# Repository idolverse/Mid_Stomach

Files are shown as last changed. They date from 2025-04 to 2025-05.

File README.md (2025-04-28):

<h1>中腹部：</h1>

本教程是关于中腹部部分的组装。

**注意** ，一旦腿做好了，这些部件肯定会被淘汰，而且是临时的。我还是把它们贴出来了，因为很多建造者都要求。这个教程里缺少图片，我把它们和硬盘一起弄丢了……

在打印所有部件之前，您应该打印一份校准器 (CALIBRATOR)，以检查部件是否能够拼合。如果您在拼合这些部件时遇到困难，可以调整切片软件的水平扩展设置来解决这个问题。此设置可能因切片机和打印机而异，但用户报告称，将其设置为 -0.15 是一个不错的起点。

填充率为 30%，壁厚为 2.5 毫米，最好无筏，无支撑（除非另有说明），大部件使用边缘以避免翘曲。

您需要打印以下所有部分：

1x BotBackLeft

1x BotBackRigt

1x BotCapLeft

1x BotCapRight

1x BotFrontLeft

1x BotFrontRigt

1x HipCoverFront

1x HipCoverLeft

1x HipCoverRight

1x MidPotHolder

2x MidWormRight

你需要两个 HS-805bb 舵机，需要进行破解。两个舵机只使用一块舵机板和一个电位器，这样两个电机就能同步旋转。教程中会详细解释这一点。

你需要65到70个滚珠轴承。你可以使用钢珠或BB枪珠。它们的直径应为6毫米。

我尝试使用Vigor VSD-11AYMB舵机，并制作了一些适合它的文件。可惜的是，这些舵机性能不佳，有时会抖动。另一个恼人的问题是，它们无法通过软件正确“分离”。

视频：https://youtu.be/9G8FDBgAxu0?t=3

<h2>步骤1：</h2>

DSC06884-600x450

检查StomGearV2.stl是否正确适合上腹部部件。



还要确保StoGearAttachV1.stl牢固地固定在 Top Stomach 部件的底面上。更多信息请查看TopStomach 教程。

<h2>步骤2：</h2>



将BotBackLeftV1.stl、BotBackRigtV1.stl、BotFrontLeftV1.stl、BotFrontRigtV1.stl组装在一起。

DSC06826-600x450

最好将它们粘在一起放在平坦的表面上。

DSC06830-600x450

对于有此需要的用户，还可以选择安装螺栓。

DSC06827-600x450

确保平面尽可能平坦。

DSC06836-600x450

如果表面太不平整，请将一张带有双面胶带的砂纸粘在平板上，然后打磨组件，直到满意为止。

DSC06886-600x450

将安装滚珠轴承的表面打磨光滑。我个人使用了丙酮，因为我的零件是用ABS打印的。



切断HipCoverFrontV1.stl上的预支撑。



用3毫米螺丝将HipCoverFrontV1.stl安装到你的组件上。我使用遮蔽胶带给黑色部分喷涂了汽车哑光喷漆。

DSC06887-600x450

用螺丝将两个MidWormRightV1.stl文件安装  到舵机摇臂上。用木螺钉将舵机安装到组件上。舵机的连接线将在后面的步骤 3中详细说明。

在此阶段，最好确保 StomGear 能够很好地与您的组件匹配。

DSC06888-600x450

在蜗轮上和 StomGear 的通孔中涂上适量的油脂。

DSC06890-600x450

检查 StomGear 上的电位器孔并将其放置在如图所示的位置。

DSC06891-600x450

适合 StomGear。

DSC06892-600x450

让它在整个组装过程中顺利进行。

<h2>步骤3：</h2>

破解伺服系统

您需要按照本教程中的说明从舵机上移除电位器。请记住，Vigor VSD-11AYMB 舵机与 Hitec805BB 舵机略有不同。以下教程针对 Hitec805BB 舵机进行说明。

需要对两个伺服器进行破解才能使其连续旋转。

两个伺服器中的一个将由另一个控制，因此您必须移除该伺服器的电路板和电位器（请妥善保管以备备用，以防有一天您烧毁了 805B 伺服器控制板）。



拆除三处焊接，拆下伺服控制板和方形电位器



将两根电线直接焊接在电机上，红点代表正极（我猜）。



并像往常一样切割阻碍伺服电机完全旋转的小块。

DSC07259-600x450

将蓝色电缆设置在电机正极侧（红点）

DSC07258-600x450

在另一个电机上，将棕色电缆设置在电机的正极侧。（红点）

DSC07257-600x450

确保已将彩色电缆与电机极性反转。这样，一个电机会朝一个方向旋转，另一个电机也会朝另一个方向旋转。

<h2>步骤4：</h2>

缺失图片：将BotCapLeftV1.stl和BotCapRightV1.stl在平面上组装在一起。如果打印 ABS，请使用丙酮；如果打印 PLA，请使用环氧树脂。

DSC06889-600x450

将电位器安装在MidPotHolderV1.stl上，并注意与小型金属定位器的位置。将MidPotHolderV1.stl粘贴到 BotCap 上。

DSC06893-600x450

将 BotCap 组件设置在主组件上。

 DSC06894-600x450

使用 4 毫米螺丝将 BotCap 固定到主组件上。

DSC06897-600x450

将TStoLowLeftV1.stl和TStoLowRightV1.stl  安装到主组件。



使用夹具压配合将使工作变得轻松。



安装 4 毫米螺钉，确保螺钉头完全嵌入部件。否则会限制上腹部和中腹部之间的旋转。

DSC06902-600x450

在侧面也添加螺丝。

<h2>步骤5：</h2>

DSC06906-600x450

在装配平板上添加适量油脂。



添加一些 6 毫米滚珠轴承，我使用了 BB 枪球，到目前为止效果很好。

DSC06909-600x450

在 TopStomach 的平板上也涂抹油脂。



安装 StomGear 以将 TopStomach 和 MidStomach 组装在一起。

DSC06912-600x450

使用 4 颗 4mm 螺丝将 StomGearV2.stl固定到StoGearAttachV1.stl ，如Top Stomach 教程中所示

DSC06913-600x450

调整螺栓，确保上腹部和中腹部紧固。但不要拧得太紧，因为我们希望这些部件能够有一定的旋转自由度。

现在是时候运行一些脚本测试来查看是否一切设置好了。

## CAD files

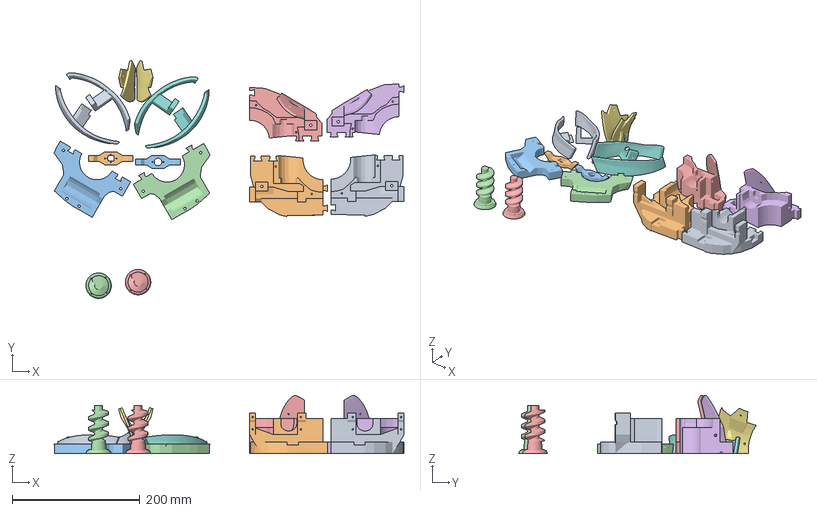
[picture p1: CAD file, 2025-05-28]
中腹部STL/中腹部.3mf
548.4 x 372.6 x 91.0 mm
BotBackLeftV1.stl
BotBackRigtV1.stl
BotCapLeftV1.stl
BotCapRightV1.stl
BotFrontLeftV1.stl
BotFrontRigtV1.stl
HipCoverFrontV1.stl
HipCoverLeftV1.stl
HipCoverRightV1.stl
MidPotHolderSquareV1.stl
MidPotHolderV1.stl
MidWormRightV1.stl x 2

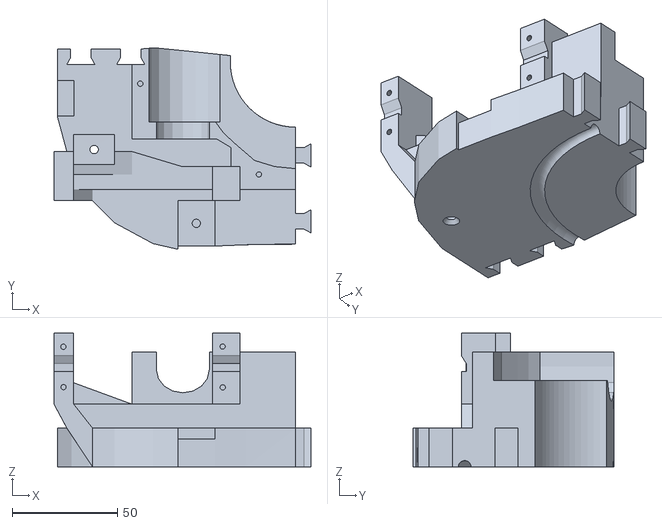
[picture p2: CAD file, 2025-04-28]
中腹部STL/BotBackRigtV1.stl
122.0 x 95.7 x 63.5

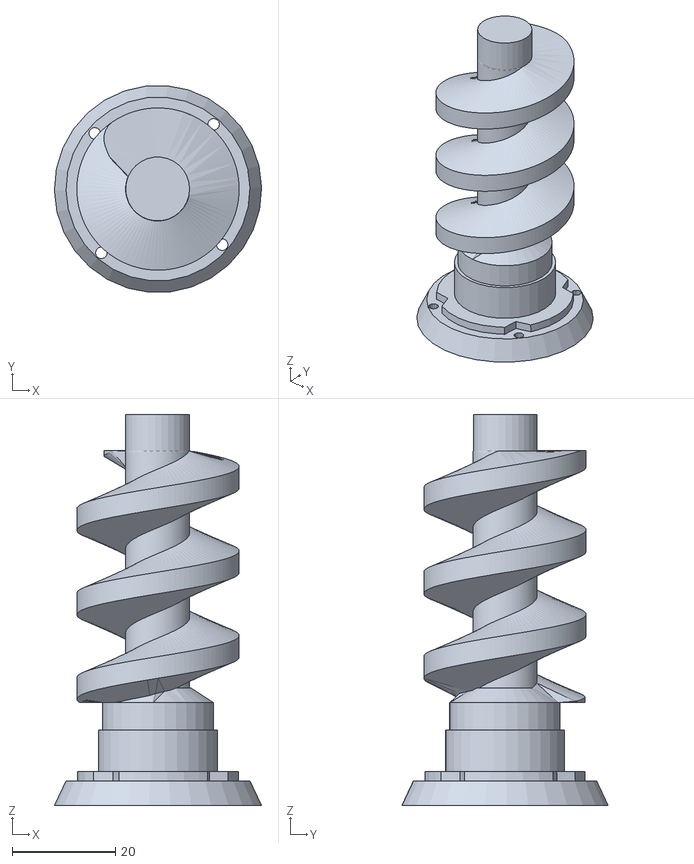
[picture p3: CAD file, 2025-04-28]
中腹部STL/MidWormRightV1.stl
40.1 x 39.9 x 75.6

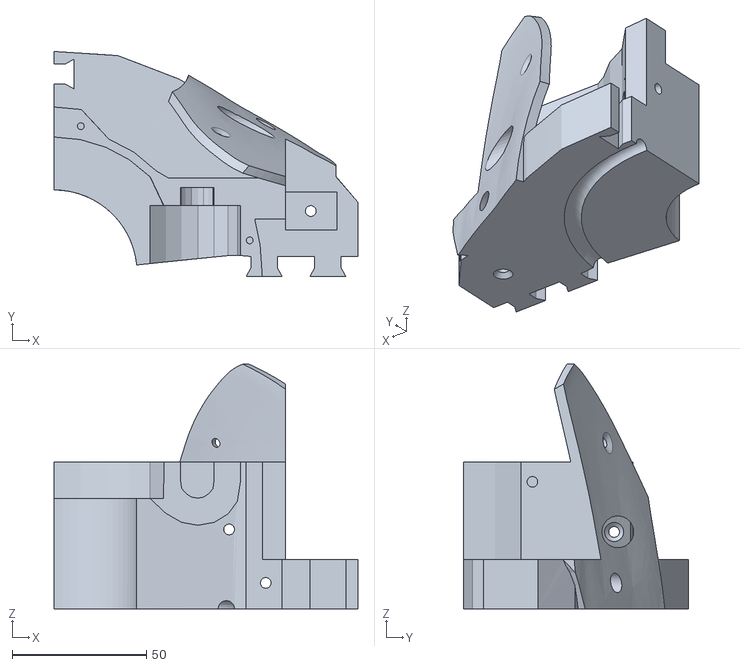
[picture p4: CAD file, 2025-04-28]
中腹部STL/BotFrontLeftV1.stl
113.0 x 83.7 x 91.0

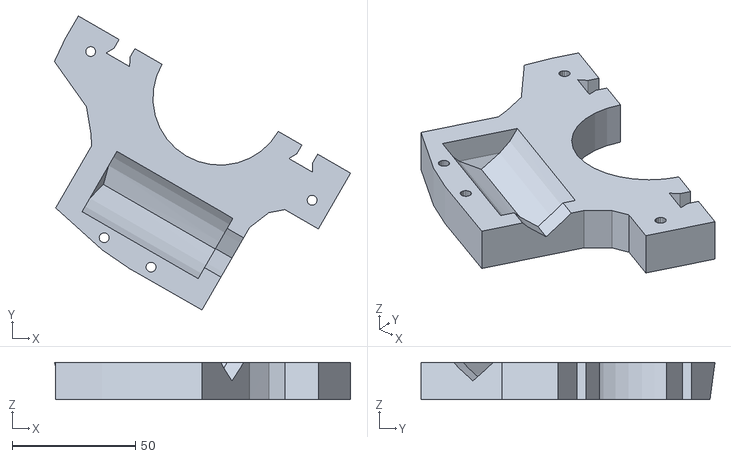
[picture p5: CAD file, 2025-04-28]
中腹部STL/BotCapLeftV1.stl
120.3 x 119.4 x 15.1

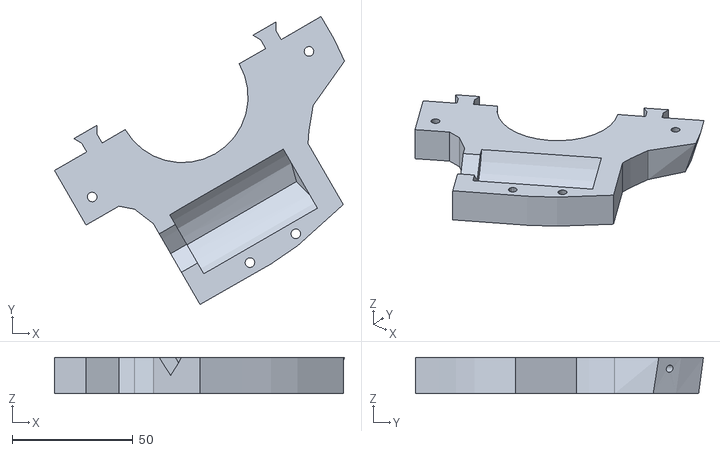
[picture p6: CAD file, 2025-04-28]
中腹部STL/BotCapRightV1.stl
120.3 x 119.4 x 15.1

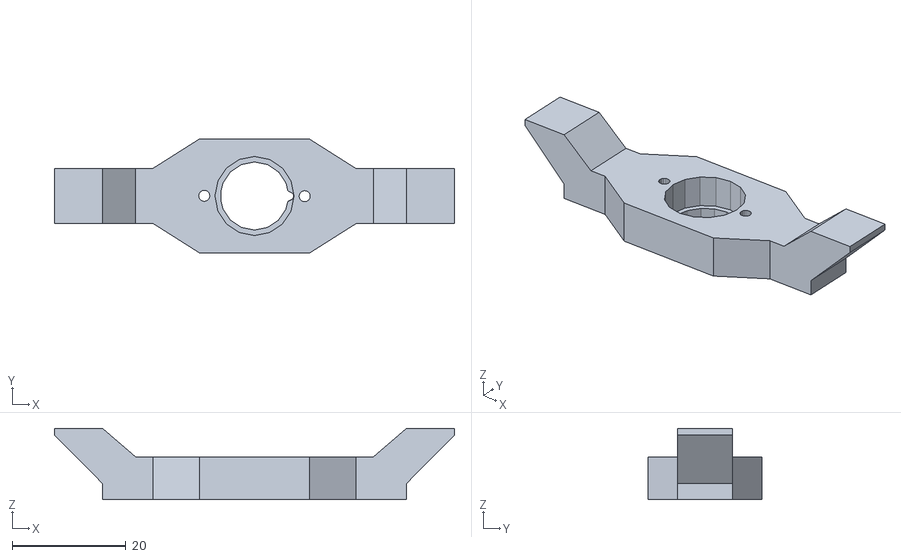
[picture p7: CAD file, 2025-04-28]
中腹部STL/MidPotHolderV1.stl
70.3 x 20.1 x 12.5

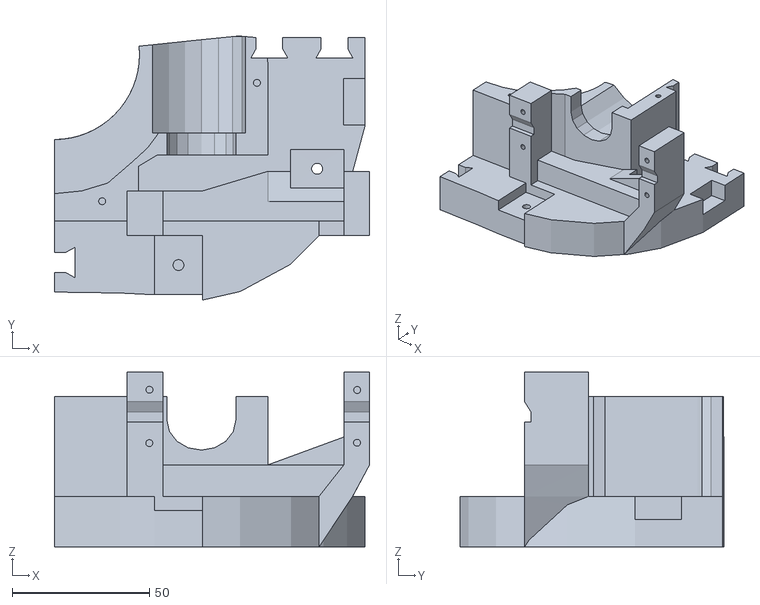
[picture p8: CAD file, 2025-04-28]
中腹部STL/BotBackLeftV1.stl
114.6 x 96.1 x 63.5

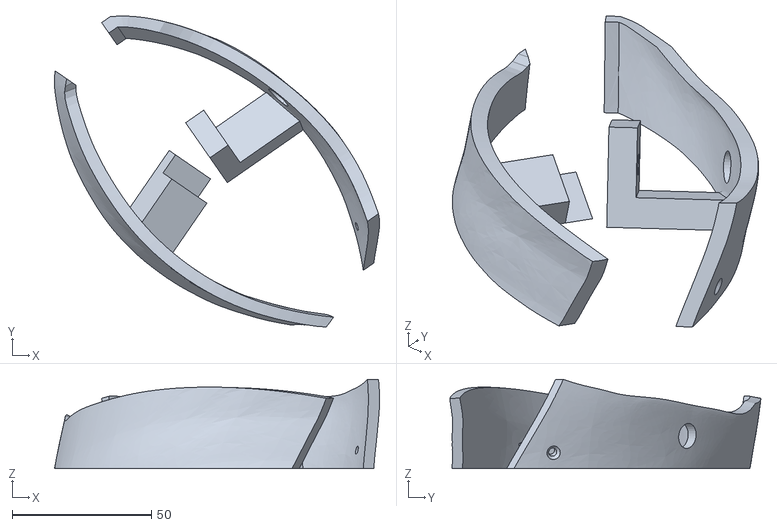
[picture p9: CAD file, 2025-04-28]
中腹部STL/HipCoverRightV1.stl
116.8 x 111.7 x 32.1

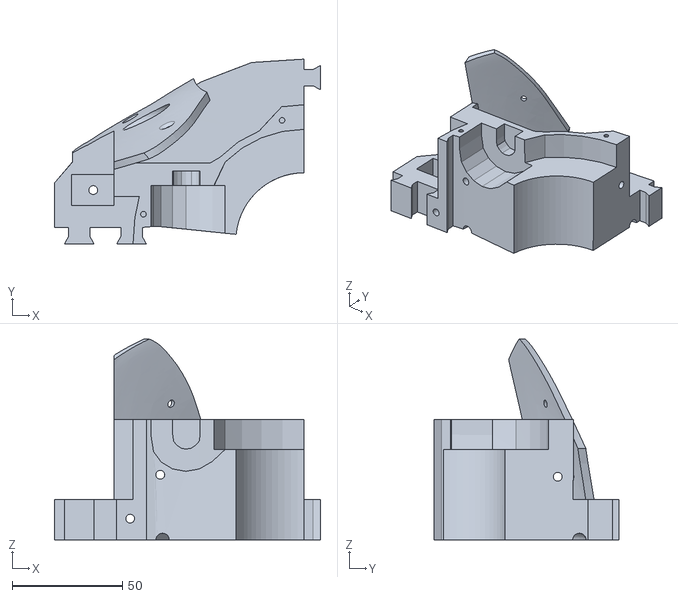
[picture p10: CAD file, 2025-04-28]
中腹部STL/BotFrontRigtV1.stl
120.5 x 83.7 x 91.0

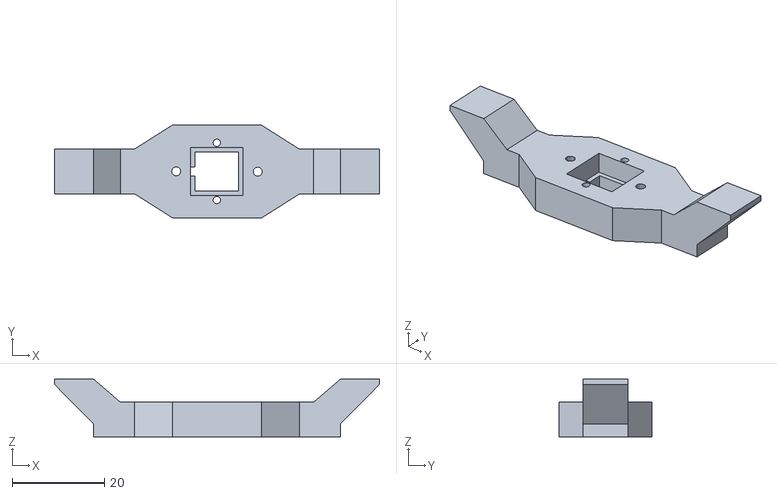
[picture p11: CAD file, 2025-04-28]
中腹部STL/MidPotHolderSquareV1.stl
70.3 x 20.1 x 12.5

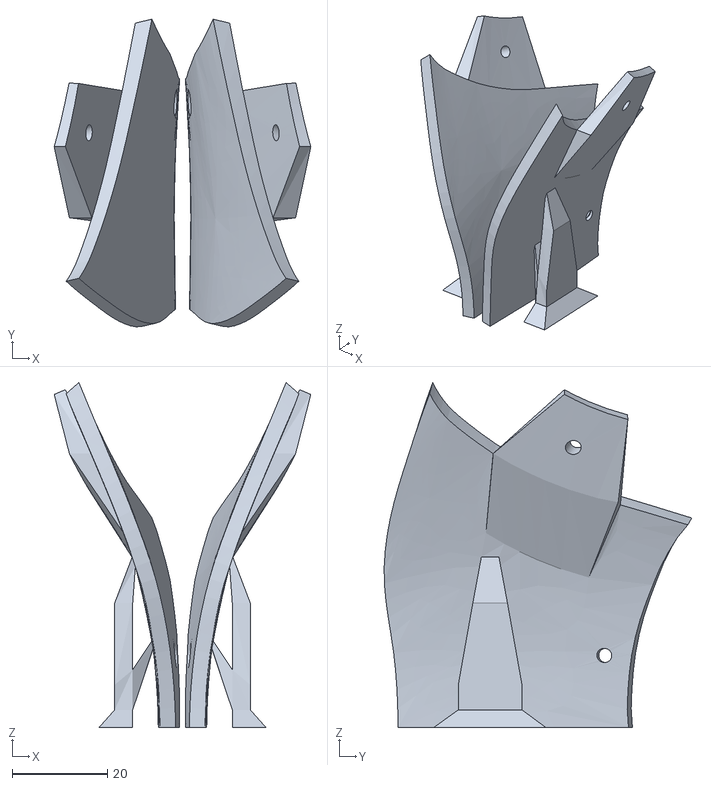
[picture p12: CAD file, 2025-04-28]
中腹部STL/HipCoverFrontV1.stl
54.0 x 64.7 x 72.5

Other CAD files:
中腹部STL/HipCoverLeftV1.stl
